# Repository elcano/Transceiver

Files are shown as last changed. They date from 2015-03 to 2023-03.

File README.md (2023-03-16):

# Transceiver
Hardware and software to support Transmit/Receive boards

The Elcano Project is an autonomous vehicle control system that runs on a stack of microprocessors, with no operating system and 
no machine learning.
Files that span more than one processor are kept in Elcano/General. The other repositories are:
Elcano/LowLevel – Drive by wire
Elcano/HighLevel – Localization, Route Finding and Pilot
Elcano/Sonar – Detects obstacles from ultrasonic sensors
Elcano/Sweep – Scanse Sweep Lidar for Obstacle Detection
Elcano/QDED – Quadrature Edge Detectors for machine vision
Elcano/Transceiver – Transmit and receive boards for remote control option

The primary autonomous vehicle control comes from HighLevel. Alternatively, the vehicle can be controlled manually, which is the function 
of the Tranceiver board. Depending on what is soldered into the board and which software is used, there are several configurations of the 
transceiver:
 
Transmitter board with joysticks and switches sending via radio.
Receiver board receiving from radio and putting information on CAN bus.
Transmitter via Bluetooth.
Receiver via Bluetooth.
Receiver from a hobbyist RC controller
User interface with joysticks and switches, putting information on CAN bus.

### Required libraries:

#### *Seeed-Studio/CAN-BUS-Shield*
Download as zip from https://github.com/Seeed-Studio/Seeed_Arduino_CAN. 
In Arduino IDE, go to Sketch -> Include Library -> Add .ZIP Library and select the .zip folder.

#### *elcano/Elcano_C2_LowLevel/Can_Protocol.h*
Download “Can_Protocol.h” from https://github.com/elcano/elcano/tree/master/Elcano_C2_LowLevel. 
Create a folder in the location where the Arduino IDE contains it’s libraries on your computer and add this file to the newly created folder.

#### *http://www.airspayce.com/mikem/arduino/RadioHead/classRH__RF69.html*
Download as zip from http://www.airspayce.com/mikem/arduino/RadioHead/index.html. 
In Arduino IDE, go to Sketch -> Include Library -> Add .ZIP Library and select the .zip folder.

#### *elcano/libraries/Settings/SettingsTemplate.h*
Download “SettingsTemplate.h” from https://github.com/elcano/elcano/tree/master/Elcano_C2_LowLevel. 
Create a folder in the location where the Arduino IDE contains it’s libraries on your computer and add this file to the newly created folder.

#### *scanse/sweep-arduino/tree/master/Sweep*
Download as zip from https://github.com/scanse/sweep-arduino. 
Note: need to unzip zip folder and then compress to zip only the sweep folder.
In Arduino IDE, go to Sketch -> Include Library -> Add .ZIP Library and select the .zip folder.

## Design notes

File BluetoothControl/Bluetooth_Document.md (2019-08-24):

# Bluetooth Modules:

###Bluetooth Transmitter
**Hardware Setup:**
1. Sparkfun SAMD21 Mini Breakout
1. HC-05 Bluetooth Modules (Master)
1. Parallax 2-Axis Joystick
1. Power supply
1. USB cable

| SPARKFUN SAMD21 MINI BREAKOUT  | PARALLAX 2-AXIS JOYSTICK | HC-05 Bluetooth  | 
| :---: | :---: | :---: |
| Pin 1 (TX) | | RX | 
| Pin 0 (RX) | | TX | 
| GND (ground) | GND (ground | GND (ground) | 
| VCC (5V) | L/R+ && U/D+ (5V) | VCC (5v) | 
| D8 (8) | | STATE | 
| D9 (9) | | EN | 
| A2 | U/D | |
| A3 | L/R | |

Bluetooth Transmitter Image Transmitter

**Software Setup:**
Bluetooth Transmitter .ino file
```c++
#include "BluetoothControlTx.h"

// initialize package
transmitterData transmitterDat;
// Utilities variables
unsigned long currTime = 0;
unsigned int counter = 0;
// Data/Buffer variables
String logger;
String dataSent;
char ackMessage; // received from the RX when it got the package
char dataBuffer[BUFFER_LIMIT];
char ackBuffer[ACK_LIMIT];

void setup()
{
    // Init hardware serial port --> PIN: 0 (RX) | 1 (TX)
    Serial1.begin(UART_BAUDRATE);
    SerialUSB.begin(UART_BAUDRATE); // Serial Monitor
    if (DEBUG)
        // wait until SerialUSB initialize
        while (!SerialUSB)
            ;

    String initMesg = "** TranX Init at " + String(UART_BAUDRATE);
    SerialUSB.println(initMesg);
    SerialUSB.println("Setup Complete!");
}

void loop()
{
    readInputs();

    // Send the values to through Bluetooh module
    String str = 'T' + String(transmitterDat.turn) + 'F' + String(transmitterDat.throttle) 
    + 'A' + String(transmitterDat.autonomous) + 'E' + String(transmitterDat.ebrake) 
    + 'R' + String(transmitterDat.reverse) + '@';
    str.toCharArray(dataBuffer, BUFFER_LIMIT);

    for (int i = 0; i < BUFFER_LIMIT; i++)
    {
        Serial1.write(dataBuffer[i]);
        SerialUSB.write(dataBuffer[i]);
    }
    SerialUSB.println();
    // Read from Bluetooh module and send to Arduino Serial Monitor
    // (Receiving ACK message from the RX)
    while (Serial1.available() > 0)
    {
        if (DEBUG)
        {
            ackMessage = Serial1.read();
            ackBuffer[counter] = ackMessage;
            counter++;
            dataBuffer[counter] = '\0'; // Keep the string NULL terminated
            SerialUSB.print(logger);
            if (ackMessage == '@') {
                break;
            }
        }
    }
    counter = 0;
    waitForProcess(100);
}

/**
 * --------------------- Helper Functions --------------------------------
 */
void readInputs()
{
    transmitterDat.turn = analogRead(TURN_PIN);
    transmitterDat.throttle = analogRead(THROTTLE_PIN);
    transmitterDat.autonomous = digitalRead(AUTO_PIN);
    transmitterDat.ebrake = digitalRead(EBRAKE_PIN);
    transmitterDat.reverse = digitalRead(REVERSE_PIN);
}

// Better version of delay() in Arduino Lib
void waitForProcess(long interval)
{
    currTime = millis();
    while (millis() < currTime + interval)
    {
        ; // Wait for "interval" ms to ensure packages are received
    }
}
```

Bluetooth Transmitter .h file
```c++
// Arduino Serial Port 
#define UART_BAUDRATE 9600 // The current TX has to be at 9600 Baurd rate so that the RX can read the data at 38400 Buard rate --- This is off, but it works for now.
#define BUFFER_LIMIT 20
#define ACK_LIMIT 5

// transmitter input pins
#define TURN_PIN A3     // joystick 2 L/R
#define THROTTLE_PIN A2 // joystick 1 U/D
#define INTERRUPT_PIN 2
#define AUTO_PIN 5
#define EBRAKE_PIN 4
#define REVERSE_PIN 20

#define NO_PACKAGE -1 // No package received
#define DEBUG 1       // Prints debugging info to serialUSB, can impact loop time                        
                      // WARNING: when true (!0), you must connect USB to allow hardware reset, otherwise
                      // SAMD21 Arduino will do nothing*/

typedef struct
{
    unsigned int throttle;
    unsigned int turn;
    bool ebrake;
    bool autonomous;
    bool reverse; // Future Stuff
} transmitterData;
```

###Bluetooth Receiver
**Hardware Setup:**
1. Sparkfun SAMD21 Mini Breakout
1. HC-05 Bluetooth Modules (Slave)
1. Power supply
1. USB cable

|  HC-05 Bluetooth | SPARKFUN SAMD21 MINI BREAKOUT  |
| --- | :---: |
| RX | Pin 1 (TX) |
| TX | Pin 0 (RX) |
| GND (ground) | GND (ground) |
| VCC (5v) | VCC (5V) |
| STATE | |
| EN | |

**Software Setup:**
Bluetooth Transmitter .ino file
```c++
#include "BluetoothControlRx.h"
//#include "Can_Protocol.h"
//#include <mcp_can.h> // using mcp_can lib from Seeed Studio

// Core Variables
receiverData receiverDat;
//MCP_CAN CAN(49); // chip selection pin for CAN. 53 for mega, 49 for our new low level board

// Utilities variables
unsigned long currTime = 0;
int turnCounter = 0;
int throttleCounter = 0;

// Data/Buffer variables
String logger;
char turnBuffer[BUFFER_LIMIT]; // char is similar to unsigned char --> which is a byte
char throttleBuffer[BUFFER_LIMIT];
char ackBuffer[ACK_LIMIT];
char dataChar;
char dividerChar;

void setup()
{
//    logger = "ACK@";
//    logger.toCharArray(ackBuffer, ACK_LIMIT);

    // Init hardware serial port --> PIN: 0 (RX) | 1 (TX)
    Serial1.begin(UART_BAUDRATE);
    SerialUSB.begin(UART_BAUDRATE); // Serial Monitor

    if (DEBUG)
        // wait until SerialUSB initialize
        while (!SerialUSB)
            ;

    // Inital CAN bus with 500KBPS baud rate (CAN_500KBPS is the baud rate)
    //    while (CAN_OK != CAN.begin(CAN_500KBPS))
    //    {
    //        if (DEBUG)
    //        {
    //            SerialUSB.println("CAN BUS Shield init fail");
    //            SerialUSB.println("Re-initializing...");
    //        }
    //        delay(1000);
    //    }

    if (DEBUG)
    {
        SerialUSB.println("CAN BUS init ok!");
        String initMesg = "** RecX Init at " + String(UART_BAUDRATE);
        SerialUSB.println(initMesg);
        SerialUSB.println("Setup Complete!");
    }
}

void loop()
{
    // Checks whether data is comming from the serial port
    while (Serial1.available() > 20)
    {
        processComingData();
        if (DEBUG)
        {
            String str = "Parsed value: T" + String(receiverDat.turn) + " F" + String(receiverDat.throttle) + " A" + String(receiverDat.autonomous) + " E" + String(receiverDat.ebrake) + " R" + String(receiverDat.reverse) + " @";
            SerialUSB.println(str);
        }
             transferToCanBus();
             //    ackMessage();
    }

}

/**
 * --------------------- Helper Functions --------------------------------
 */

// Gather/Process data and put it into dataBuffer buffer for parsing
void processComingData()
{
    dataChar = Serial1.read(); // Reads the data from the serial port
    dataParser();
}

// Parse the completed data buffer from the transmitter
void dataParser()
{

    if (dataChar == 'T' || dataChar == 'F' || dataChar == 'A' || dataChar == 'E' || dataChar == 'R' || dataChar == '@')
    {
        dividerChar = dataChar;
    }

    // Start parsing data byte
    if ((dividerChar == '@') || (dividerChar != dataChar))
    {
        switch (dividerChar)
        {
        case 'T': // Parsing Turn
            if (DEBUG_PARSE)
                SerialUSB.println("T - " + String(dataChar));
            turnBuffer[turnCounter] = dataChar;
            turnCounter++;
            turnBuffer[turnCounter] = '\0'; // Keep the string NULL terminated
            break;
        case 'F': // Parsing Throttle
            if (DEBUG_PARSE)
                SerialUSB.println("F - " + String(dataChar));
            throttleBuffer[throttleCounter] = dataChar;
            throttleCounter++;
            throttleBuffer[throttleCounter] = '\0'; // Keep the string NULL terminated
            break;
        case 'A': // Parsing Autonomous
            if (DEBUG_PARSE)
                SerialUSB.println("A - " + String(dataChar));
            if (dataChar == '1')
                receiverDat.autonomous = true;
            else
                receiverDat.autonomous = false;
            break;
        case 'E': // Parsing Ebrake
            if (DEBUG_PARSE)
                SerialUSB.println("E - " + String(dataChar));
            if (dataChar == '1')
                receiverDat.ebrake = true;
            else
                receiverDat.ebrake = false;
            break;
        case 'R': // Parsing Reverse
            if (DEBUG_PARSE)
                SerialUSB.println("R - " + String(dataChar));
            if (dataChar == '1')
                receiverDat.reverse = true;
            else
                receiverDat.reverse = false;
            break;
        case '@': // Reaching the end of line
            if (dataChar == '@')
            {
                if (DEBUG_PARSE)
                    SerialUSB.println("EOT - " + String(dataChar));

                // update turn and throttle struct
                receiverDat.turn = atoi(turnBuffer);
                receiverDat.throttle = atoi(throttleBuffer);

                // reset all counter and buffer
                turnCounter = 0;
                throttleCounter = 0;
                turnBuffer[turnCounter] = NULL;
                throttleBuffer[throttleCounter] = NULL;
            }
            break;
        default:
            if (DEBUG_PARSE)
                SerialUSB.println("Default - " + String(dataChar));
            break;
        }
    }
}

// Process the data over the CAN BUS protocal
void transferToCanBus()
{
    if (DEBUG)
    {
        SerialUSB.println("Sending data to CAN BUS...");
    }

    //    CAN.sendMsgBuf(RCDrive_CANID, 0, BUFFER_LIMIT, (char *)&receiverDat); // RCDrive_CANID or RCStatus_CANID i dont know...
    //    wait(100);
}

// ACKNOWLEDGE the data received
void ackMessage()
{
    SerialUSB.println();
    if (Serial1.available())
    {
        Serial1.print("ACK");
    }
}

// Better version of delay() in Arduino Lib
void wait(long interval)
{
    currTime = millis();
    while (millis() < currTime + interval)
    {
        ; // Wait for "interval" ms to ensure packages are received
    }
}

```

Bluetooth Receiver .h file
```c++
// Arduino Serial Port 
#define UART_BAUDRATE 38400
#define BUFFER_LIMIT 20
#define ACK_LIMIT 5

// Arduino Debugger
#define NO_PACKAGE -1 // No package received
#define DEBUG_PARSE 0 // This debug only for process coming data function
#define DEBUG 1       // Prints debugging info to serialUSB, can impact loop time                        
                      // WARNING: when true (!0), you must connect USB to allow hardware reset, otherwise
                      // SAMD21 Arduino will do nothing*/

// Data struct of packages being sent
typedef struct
{
    unsigned int throttle;
    unsigned int turn;
    bool ebrake;
    bool autonomous;
    bool reverse; // Future Stuff
} receiverData;

#define RCStatus_CANID 0x50
#define HiStatus_CANID 0x100
#define LowStatus_CANID 0x200
#define RCDrive_CANID 0x300
#define HiDrive_CANID 0x350
#define Actual_CANID 0x500
```

### References/Tip
1. Sparkfun SAMD21 Mini Breakout hook up guide: https://learn.sparkfun.com/tutorials/samd21-minidev-breakout-hookup-guide/samd21-mini-breakout-overview
1. If the receiver gets a reverse question mark, it might because of both the receiver and the transmitter Baud Rate are not configured at the same rate. Please try Baud Rate: 38400 (on the Receiver) and 9600 (on the Transmitter) and vice versa to see if the outcome is any better.

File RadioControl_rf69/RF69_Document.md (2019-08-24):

# Note for future implementations:
1. If the board got an error or undetectable by any computer after uploading the code, **__Double Click the reset button__** at the end of the SAMD21 Module to refresh the whole board.

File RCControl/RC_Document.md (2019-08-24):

# RC Modules Documentation

**Hardware Setup for RC Receiver:**
Required hardware: 
1. Sparkfun SAMD21 Mini Breakout
2. Spektrum AR610X Receiver
3. Power supply
4. USB cable

| SPEKTRUM AR610X  | SPARKFUN SAMD21 MINI BREAKOUT  |
| --- | :---: |
| AUX1 | 7 |
| GEAR | 8 |
| RUDD | 0 |
| ELEV | 1 |
| AILE | 6 |
| THRO | 9 |
| BND/BRA | NA (Use for Binding only) |

The RC code utilizes the `attachInterrupt()` from Arduino to detect different in frequency that the board is receiving while the controller values change. This is almost similar to an `async` which will optimize the code so that we won't have to constantly check for data every iteration in the `loop()`.

Whenever the RC receiver gets a signal, the value will go high and activate the `attachInterrupt()` to keep track when the value return back to low. Once it completed this step, the time period where the change is recordeded will be the value of each switches on the Receiver channels.

# Note for future implementations:
1. The CAN BUS Protocol is written with the RC code; however, the CAN BUS has yet been tested at this moment. Recommend finding a way to test current CAN BUS connection for the RC code.
2. There is a __Note__  section in the main `Loop()` of the RCControlRx.ino. This Note is there for the future implementation where the CAN BUS passed the data to other Low/High level board and received the ACK message back. Without setting the `receiverData.newData = false;` the RC code might not be able to receive new data coming from the RC controller. 
3.

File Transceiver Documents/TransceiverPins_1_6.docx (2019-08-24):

Elcano Transceiver Board

Arduino | Bluetooth | RC receiver | Rfm69rcw Radio | CAN 2515 | Receiver Controls | Transmitter Controls
D0 RX | RX1 | CH3_A
D1 TX | TX0 | CH4_A
D2 | | | | CAN_INT
D3 | | | | CAN_SS
D4 | | | | | E-stop | E-stop
D5 | | | | | Manual/Auto | Manual/Auto
D6 | | CH5_A | Radio OK LED | | | Radio Ok led
D7 | MOD | CH1_A
D8 | CTS | CH2_A
D9 | RTS | CH6_A
D10 SS | | | Radio_SS
D11 MOSI | | | MOSI | MOSI
D12 MISO | | | MISO | MISO
D13 SCK | | | SCK | SCK
D20 | | | | | Reverse | Reverse
D21 | | | Radio Interrupt
A0 | | | | | 2 Up-Dn / Center
A1 | | | | | 1 L-R / center | 1 L-R / center
A2 | | | | | 1 Joystick Up-Dn | 1 Joystick Up-Dn
A3 | | | | | 2 Joystick L-R | 2 Joystick L-R
RESET | | | Reset | | | Reset sw
Vin (5V)
Vcc (3.3V) | Vin = 3.3V | 3.3V | 3.3V | 3.3V | 3.3V | 3.3V
GND | GND | GND | GND | GND | GND | GND
AREF to 3.3V

Gray shaded columns are mutually exclusive; so are blue shaded columns.

Transmitter board will not have CAN or RC receiver. Transmitter switches shall incorporate LEDs that indicate their state.
Receiver may have all components, but normally will use only one of Radio, Bluetooth or RC receiver.

Arduino: Sparkfun SAMD21: https://www.sparkfun.com/products/13664

Radio: SparkFun parts 12775, 14875, 592: https://www.sparkfun.com/products/12775 ,
http://www.orcam.eu/res/Datablad/rf69v12.pdf

Bluetooth: Adafruit Bluefruit: https://www.adafruit.com/product/2479?gclid=EAIaIQobChMI_Iv29-CR4AIVi8JkCh0fKwybEAYYASABEgKXWfD_BwE

RC Receiver: Spektrum AR610: https://spektrumrc.com/Products/Default.aspx?ProdId=SPM6700

Level shifter: https://www.addicore.com/TXS0108E-p/ad284.htm

An equivalent level shifter is https://www.adafruit.com/product/395?gclid=EAIaIQobChMIk7nvup_Q4AIVER6tBh0WywndEAQYAiABEgJw7fD_BwE

CAN: MCP 2515 http://ww1.microchip.com/downloads/en/devicedoc/21801e.pdf and
MCP 2551 http://ww1.microchip.com/downloads/en/devicedoc/21667d.pdf

Controls: Two joysticks and three toggle switches. Toggle switches have built-in LEDs to show their state. There is also an LED connected to power.

Bluetooth and RC Receiver use separate physical socket:
Bluetooth 8 pins: Mod, CTS, TX0, RX1, Vin, RTS, GND, DFU

RC receiver 7 pins: Ch1, Ch2, Ch3, Ch4, Ch), Ch6, BND
RC receiver also has 7 rows of power and 7 rows of ground forming a 3x7 socket.

Pin view is top view of the transceiver board or bottom view of RC Receiver

Gnd | Gnd | Gnd | Gnd | Gnd | Gnd | Gnd
5V | 5V | 5V | 5V | 5V | 5V | 5V
Ch1_B | Ch2_B | Ch3_B | Ch4_B | Ch5_B | Ch6_B | BND

ChX Signals from RC Receiver will need to be converted from 5V to 3.3V. This is the only voltage conversion needed on the transceiver board. At present, neither of the receivers will bind or respond to the Spektrum transmitter.

The level shifter is connected with VB to 5V, and VA and OE to 3.3V. On the level shifter, channels A 1-6 are 3.3V signals connected to the Arduino. Channels B 1-6 are 5V signals connected to the RC receiver socket. Channels 7 and 8 are not used.

There is a jumper to set the Radio reset to either D6 or Arduino RESET.

~~JB:~~ ~~tx~~ ~~and~~ ~~rx~~ ~~sketch resets RF69 radio on D6 but radio reset should not connect electrically to Arduino reset so we can~~ ~~perform a radio reset in software by toggling the pin.~~
D6 is jumpered to either Radio OK LED or RC Receiver CH5.

There may be two joysticks. Jumpers select which axes are used. There are several configurations

1. Up to two joysticks that do not return a center value. Software may choose to process only the left-right reading from one and only the up-down reading from the other.
1. Two joysticks returning center values. One produces a left-right reading and the other produces up-down.
2. A single joystick returning a center value, a left-right, and an up-down signal.

Board has an input jack for 9 to 12V DC, which is put through regulators to produce 5V and 3.3V. All parts (except RC receiver) run from 3.3V. The 2551 will use 5V for CAN transmission.

CANRX and CAN_RXD are the same. CANTX and CAN_TXD are the same.
The signals CANH and CANL are the outputs to the CAN bus connector.

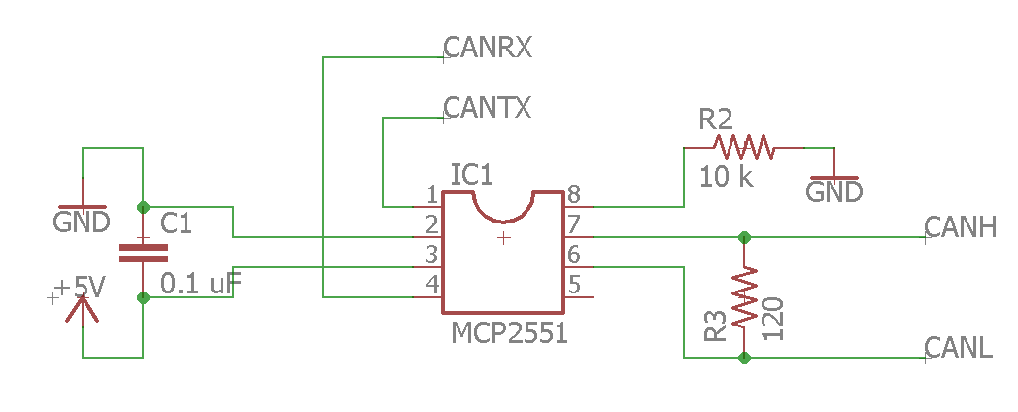
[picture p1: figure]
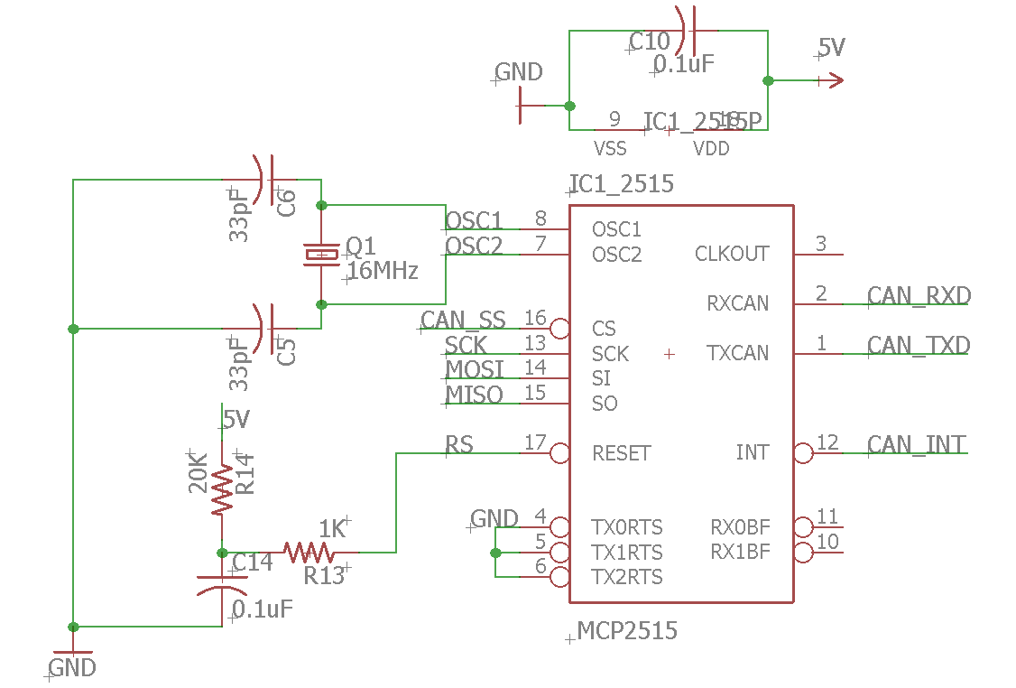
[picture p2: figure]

Rev 1.6 Feb 22, 2019

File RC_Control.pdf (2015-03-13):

# RC Control

# CSS 427: Final Report

## Brad Minogue, Carl Martinez, Amit Moolani, Alexander Yelle, Enoch Fu

Implementation of a remote control subsystem for an Elcano tricycle.

# RC Control

## CSS 427: Final Report

# Introduction

This project led to the implementation of a remote control subsystem for use on an Elcano tricycle. Using the knowledge and experience that we gained in previous labs and lectures we were able to fully integrate a remote control into the steering, accelerating, and braking of an Elcano tricycle. An Arduino with a DAC connected acted as the gateway from the RC receiver to the servo-motor and

## throttle. The process took 3 weeks to complete, each week accomplishing a different goal:

1. Adding throttle connectivity to the trike.
2. Writing and testing code to translate RC input data to correct PWM signals.
3. Hooking up the Arduino to the trike, testing functionality.

# Problems Addressed

## - Adding Throttle Capability

## The project started with troubleshooting the throttle connection on the trike. Everything

appeared to be wired correctly but we would get no response from the throttle. We had to test every connection and power source to find the root of the problem. After testing all existing

## connections and finding nothing wrong we had to turn to the manual to find out why the throttle was not working. The end result was that the control power supply pin was not

connected. After making the appropriate connection the trike gained throttle capabilities.

## - RC Receiver Connection

We used the left joystick from the RC receiver to receive input for acceleration, steering and braking. Right and left for steering, forward and backward for acceleration and braking. Attaching the RC receiver to an Arduino allowed us to translate the inputs into a PWM signal to control the servo-motor and throttle. We wrote code to make a linear translation from RC

## input to the PWM signal. A DAC was attached to the Arduino to allow for correct throttle

output.

## - Calibration of Input and Output

Using existing code we already had the range of numbers for the output values. The RC input required testing to find the maximum and minimum values for steering, braking, accelerating, and how large the dead zone should be.

## - Bike Connections

## We then were able to connect our programmed Arduino to the shield connected to the yellow

trike. The trike had battery packs to provide the Arduino and motors with power.

## Connections existed from the motors to a breadboard that sat on the trike. After reading through schematics and checking connections with the previous setup, we connected our RC

receiver to get power from the Arduino’s 5V output. We also connected the Channels 1 and 2 from the receiver to be read into pins 2 and 3 of the Arduino. These gave the RC transmitted the ability to control the steering and braking of the trike respectively. We then connected the motor’s steering and braking input pins to the Arduino’s steering and braking output pins.

## These were pins 6 and 7 on the Arduino respectively. Then the throttle wires had to be

snipped and connected to the 5V and GND pins of the Arduino. The input for the throttle was

## connected to the Arduino via pin 12 on the 15 pin DAC. Once those connections were made

and the trike was fastened and powered up, we were able to confirm the working of our trike.

## - Brakes

The braking system of the trike had been manipulated in the past, restricting its functioning. We were able to find the loose connection in the brake that did not allow the brake to ever

## fully compress over the wheel to give it adequate braking. We attempted to fix this by tightening the brake wires and moving the location of the pivot holding the brakes to the brake system motor. After an hour and a half of debugging we were able to mildly improve

the system, but still needs much more work to be able to work to the full of its capability.

# Code

//RC_Control.ino
#include <SPI.h>

//RC input values
const int DEAD_ZONE = 75;
const int ACC_START = 1322; const int TURN_START= 1322; //max brake
const int MIN_ACC = 911;
//full throttle
const int MAX_ACC = 1730;
//max turn left
const int MIN_TURN = 911;
//max turn right
const int MAX_TURN = 1733;

//OUTPUT values
const int MIN_ACC_OUT = 40; const int MAX_ACC_OUT = 227;

const int MIN_BRAKE_OUT = 167; const int MAX_BRAKE_OUT = 207;

const int LEFT_TURN_OUT = 126; const int RIGHT_TURN_OUT = 250; const int STRAIGHT_TURN_OUT = 187;

//ARDUINO PIN SELECTORS
const int TURN_PIN = 2;
const int ACC_PIN =3;
const int ACC_OUT_PIN = 5;
const int STEER_OUT_PIN = 6;
const int BRAKE_OUT_PIN = 7;
const int SelectCD | = 49; // Select IC 3 DAC (channels C and D)
const int SelectAB | = 53; // Select IC 2 DAC (channels A and B)

void setup()
{ //Set up pins
pinMode(ACC_OUT_PIN, OUTPUT);
pinMode(BRAKE_OUT_PIN, OUTPUT); pinMode(STEER_OUT_PIN, OUTPUT);
// SPI: set the slaveSelectPin as an output: pinMode (SelectAB, OUTPUT);
pinMode (SelectCD, OUTPUT);
pinMode (10, OUTPUT);

SPI.setDataMode( SPI_MODE0);
SPI.setBitOrder( MSBFIRST);
// initialize SPI:
// The following line should not be neccessary. It uses a system library. PRR0 &= ~4; // turn off PRR0.PRSPI bit so power isn't off
SPI.begin();
for (int channel = 0; channel < 4; channel++)
DAC_Write (channel, 0); // reset did not clear previous states

Serial.begin(9600);
}
//Checks for each input: accelerating, turning, braking
void loop() {
//Steering
int test = pulseIn(TURN_PIN, HIGH,25000); if(testTurn(test))
{
//Serial.print("turn: ");
//Serial.println(convertTurn(test)); steer(convertTurn(test));
}
else
{
steer(STRAIGHT_TURN_OUT);
}
//Braking
test = pulseIn(ACC_PIN, HIGH,25000); if(testBrake(test))
{
//Serial.print("braking: "); //Serial.println(convertBrake(test)); brake(convertTurn(test));
}
else
{
brake(MIN_BRAKE_OUT);
}
//Accelerating
if(testAcc(test))
{
//Serial.print("Acc: ");
//Serial.println(convertThrottle(test)); moveVehicle(test);
}
else
{
moveVehicle(MIN_ACC_OUT);
}
delay(50);
}
//Converts RC values to corresponding values for the DAC int convertTurn(int input)
{
//full turn right = 250, full turn left = 126
int dacRange = RIGHT_TURN_OUT - LEFT_TURN_OUT; int rcRange = MAX_TURN - MIN_TURN;
input-= MIN_TURN;
double output = (double)input /(double)rcRange; //swap left and right
output = 1 - output;
output *= dacRange;
output += LEFT_TURN_OUT;
//set max and min values if out of range int trueOut = (int)output;
if(trueOut > RIGHT_TURN_OUT)
trueOut = RIGHT_TURN_OUT;
else if(trueOut < LEFT_TURN_OUT) trueOut = LEFT_TURN_OUT;
return trueOut;

}
int convertBrake(int input)
{
//full brake = 207, min = 167
const int dacRange = MAX_BRAKE_OUT - MIN_BRAKE_OUT; const int rcRange = (ACC_START - DEAD_ZONE) - MIN_ACC; input -= MIN_ACC;
double output = (double)input /(double)rcRange; output *= dacRange;
output += MIN_BRAKE_OUT;
//set min values if out of range
int trueOut = (int)output; if(trueOut < MIN_BRAKE_OUT) trueOut = MIN_BRAKE_OUT;
return trueOut;
}
int convertThrottle(int input)
{
//full throttle = 227, min = 40
const int dacRange = MAX_ACC_OUT - MIN_ACC_OUT; const int rcRange = MAX_ACC - (ACC_START + DEAD_ZONE); input -= (ACC_START + DEAD_ZONE);
double output = (double)input /(double)rcRange; output *= dacRange;
output += MIN_ACC_OUT;
//set max values if out of range
int trueOut = (int)output; if(trueOut > MAX_ACC_OUT)
trueOut = MAX_ACC_OUT;
return trueOut;
}

//Tests for inputs
boolean testTurn(int turn)
{
return (turn > ACC_START + DEAD_ZONE || turn < ACC_START - DEAD_ZONE); }
boolean testAcc(int acc)
{
return (acc > ACC_START + DEAD_ZONE); }
boolean testBrake(int brake)
{
return (brake < ACC_START - DEAD_ZONE); }
//Send values to output pin
void steer(int pos)
{
analogWrite(STEER_OUT_PIN, pos); }
void brake(int amount)
{
analogWrite(BRAKE_OUT_PIN, amount); }
void moveVehicle(int acc)
{
/* Observed behavior on ElCano #1 E-bike no load (May 10, 2013, TCF)
0.831 V at rest | 52 counts
1.20 V: nothing | 75
1.27 V: just starting 79
1.40 V: slow, steady 87
1.50 V: brisker | 94
3.63 V: max | 227 counts
255 counts = 4.08 V
*/
DAC_Write(0, acc);
}
/*---------------------------------------------------------------------------------------*/ /* DAC_Write applies value to address, producing an analog voltage.

// address: 0 for chan A; 1 for chan B; 2 for chan C; 3 for chan D // value: digital value converted to analog voltage
// Output goes to mcp 4802 Digital-Analog Converter Chip via SPI // There is no input back from the chip.
*/
void DAC_Write(int address, int value)

/*
REGISTER 5-3: WRITE COMMAND REGISTER FOR MCP4802 (8-BIT DAC) A/B — GA SHDN D7 D6 D5 D4 D3 D2 D1 D0 x x x x
bit 15 | bit 0
bit 15 | A/B: DACA or DACB Selection bit
1 = Write to DACB
0 = Write to DACA
bit 14 | — Don’t Care
bit 13 | GA: Output Gain Selection bit
1 = 1x (VOUT = VREF * D/4096)
0 = 2x (VOUT = 2 * VREF * D/4096), where internal VREF = 2.048V.
bit 12 SHDN: Output Shutdown Control bit
1 = Active mode operation. VOUT is available.
0 = Shutdown the selected DAC channel. Analog output is not available at the channel that was shut down.
VOUT pin is connected to 500 k (typical)
bit 11-0 D11:D0: DAC Input Data bits. Bit x is ignored.

With 4.95 V on Vcc, observed output for 255 is 4.08V.
This is as documented; with gain of 2, maximum output is 2 * Vref

*/

{
int byte1 = ((value & 0xF0)>>4) | 0x10; // acitve mode, bits D7-D4
int byte2 = (value & 0x0F)<<4; | // D3-D0
if (address < 2)
{
// take the SS pin low to select the chip: digitalWrite(SelectAB,LOW);
if (address >= 0)
{
if (address == 1)
byte1 |= 0x80; // second channnel SPI.transfer(byte1);
SPI.transfer(byte2);
}
// take the SS pin high to de-select the chip: digitalWrite(SelectAB,HIGH);
}
else
{
// take the SS pin low to select the chip: digitalWrite(SelectCD,LOW);
if (address <= 3)
{
if (address == 3)
byte1 |= 0x80; // second channnel SPI.transfer(byte1);
SPI.transfer(byte2);
}
// take the SS pin high to de-select the chip: digitalWrite(SelectCD,HIGH);
}
}

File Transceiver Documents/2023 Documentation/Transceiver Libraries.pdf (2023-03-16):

Transceiver Libraries Required

This document outlines the required libraries for each .ino file in the Transceiver repository. A list of all required libraries and links with instructions for download are shown below, as well as an in-depth specification for each .ino file. The github for these files can be found here https://github.com/elcano/Transceiver with current changes found here https://github.com/jacrys3/Transceiver.

Required libraries:
Seeed-Studio/CAN-BUS-Shield
Download as zip from https://github.com/Seeed-Studio/Seeed_Arduino_CAN
In Arduino IDE, go to Sketch -> Include Library -> Add .ZIP Library and select the .zip folder

elcano/Elcano_C2_LowLevel/Can_Protocol.h
Download “Can_Protocol.h” from https://github.com/elcano/elcano/tree/master/Elcano_C2_LowLevel
Create a folder in the location where the Arduino IDE contains it’s libraries on your computer and add this file to the newly created folder.

http://www.airspayce.com/mikem/arduino/RadioHead/classRH__RF69.html
Download as zip from http://www.airspayce.com/mikem/arduino/RadioHead/index.html
In Arduino IDE, go to Sketch -> Include Library -> Add .ZIP Library and select the .zip folder

elcano/libraries/Settings/SettingsTemplate.h
Download “SettingsTemplate.h” from https://github.com/elcano/elcano/tree/master/Elcano_C2_LowLevel
Create a folder in the location where the Arduino IDE contains it’s libraries on your computer and add this file to the newly created folder.

scanse/sweep-arduino/tree/master/Sweep
Download as zip from https://github.com/scanse/sweep-arduino
Note: need to unzip zip folder and then compress to zip only the sweep folder
In Arduino IDE, go to Sketch -> Include Library -> Add .ZIP Library and select the .zip folder

BluetoothControlRx.ino
Seeed-Studio/CAN-BUS-Shield
elcano/Elcano_C2_LowLevel/Can_Protocol.h

BluetoothControlTx.ino
None

lidar.ino
Seeed-Studio/CAN-BUS-Shield elcano/Elcano_C2_LowLevel/Can_Protocol.h scanse/sweep-arduino/tree/master/Sweep

RadioControl_rf69.ino
http://www.airspayce.com/mikem/arduino/RadioHead/classRH__RF69.htmlSeeed-Studio/CAN-BUS-Shield

RCControlRx.ino
Seeed-Studio/CAN-BUS-Shield elcano/Elcano_C2_LowLevel/Can_Protocol.h elcano/libraries/Settings/SettingsTemplate.h

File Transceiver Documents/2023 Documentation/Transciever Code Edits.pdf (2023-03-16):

Transceiver Code Edits

This document contains any edits made to the Transceiver code given in https://github.com/elcano/Transceiver. These changes can be seen respectively in https://github.com/jacrys3/Transceiver.

BluetoothControlRx.ino - Compiles
1. All uses of “SerialUSB” have been changed to “Serial3”
2. Fixed an issue where some semi-colons were missing when pre-declaring functions “sendToCanBus” and “receiveFromCanBus”
3. Creation of CAN object needs to be of type “mcp2515_can”, not “MCP_CAN”
4. In sendToCanBus() method, need to reference MCP_CAN when using sendMsgBuff
5. Need to include “mcp2515_can.h” and “mcp2515_can_dfs.h”

BluetoothControlTx.ino - Compiles
1. All uses of “SerialUSB” have been changed to “Serial3”

Lidar.ino - Compiles
1. All uses of “lidarMSGBuffer” have been changed to “lidarStruct”
2. Creation of CAN object needs to be of type “mcp2515_can”, not “MCP_CAN”
3. In sendToCanBus() method, need to reference MCP_CAN when using sendMsgBuff
4. Need to include “mcp2515_can.h” and “mcp2515_can_dfs.h”

RadioControl_rf69.ino - Compiles
1. All uses of “SerialUSB” have been changed to “Serial3”
2. All uses of “analogReadResolution” have been changed to “analogRead”
3. RH_RF69 has been changed to RC_RF69_H
4. Creation of CAN object needs to be of type “mcp2515_can”, not “MCP_CAN”
5. Need to include “mcp2515_can.h” and “mcp2515_can_dfs.h”

RCControlRx.ino - Compiles
1. All uses of “SerialUSB” have been changed to “Serial3”
2. Creation of CAN object needs to be of type “mcp2515_can”, not “MCP_CAN”
3. In sendToCanBus() method, need to reference MCP_CAN when using sendMsgBuff
4. Need to include “mcp2515_can.h” and “mcp2515_can_dfs.h”

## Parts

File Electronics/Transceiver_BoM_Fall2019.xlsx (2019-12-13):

 |  | Board Manufacturer Specs | rvc RC | xmit BT | rcv BT | xmit radio | rcv radio
 | Traces are 15 mil | Board needs 2 oz copper |  |  |  |  |  |  | Two Layers: Front & Back
 |  | Through hole components
Qty | Device Name | Value |  |  |  |  |  | In BoM? | Digikey Part Number | Package | Part Label | Description | DESCRIPTION | External Link | DIGI-KEY_PURCHASE_URL | MANUFACTURER_PART_NUMBER | MF | MP | MPN | OC_FARNELL | OC_NEWARK | PACKAGE | PROD_ID | SF_SKU | SPICEPREFIX | VALUE | VENDOR
5 | PINHD-1X2 | SAMD21 | 1 | 1 | 1 | 1 | 1 | yes | 732-5315-ND | 1X02 | 5V TEST,3.3V TEST, JUMPER, RADIO-OK | PIN HEADER |  |  | https://www.digikey.com/products/en?keywords=732-5315-ND
5 | PINHD-1X3 | Rcvr (Pwr/Reset) XMIT+(auto/E_stop/Rev) 2 |  | 5 | 2 | 5 | 2 | yes | 732-5316-ND | 1X03 | REST SW,POWER SW,AUTO MNL,ESTOP,REVERSE | PIN HEADER |  |  | https://www.digikey.com/products/en?keywords=%20732-5316-ND
2 | PINHD-1X4 | JoyStick L/R | 0 | 2 | 0 | 2 | 0 | yes | 732-5317-ND | 1X04 | LEFT JOY STICK, RIGHT JOYSTICK | PIN HEADER |  |  | https://www.digikey.com/products/en?keywords=732-5317-ND
2 | PINHD-1X6 | BLUETOOTH Module | 0 | 1 | 1 | 0 | 0 | yes | S5481-ND | 1X06 | HC-05 BLUETOOTH | PIN HEADER | Right Angle Female PIN Header |  | https://www.digikey.com/product-detail/en/sullins-connector-solutions/PPPC061LGBN-RC/S5481-ND/775939
3 | PINHD-1X7 | RC rcvr | 3 | 0 | 0 | 0 | 0 | yes | S7040-ND | 1X07 | RC-RECEIVER | PIN HEADER | Female pin header |  | https://www.digikey.com/product-detail/en/sullins-connector-solutions/PPPC071LFBN-RC/S7040-ND/810179
2 | PINHD-1X8 | RF Module | 0 | 0 | 0 | 2 | 2 | yes | S7006-ND | 1X08 | RFM-69 pins | PIN HEADER | Female pin header |  | https://www.digikey.com/product-detail/en/sullins-connector-solutions/PPTC081LFBN-RC/S7006-ND/810147
2 | PINHD-1X10 | Voltage Converter | 2 | 2 | 2 | 0 | 0 | yes | S7008-ND | 1X10 | Logic convertor Pins | PIN HEADER | Female pin header |  | https://www.digikey.com/product-detail/en/sullins-connector-solutions/PPTC101LFBN-RC/S7008-ND/810149
2 | PINHD-1X12 | SAMD21 | 2 | 2 | 2 | 2 | 2 | yes | S6100-ND | 1X12 | SAMD 21 pins | PIN HEADER | Female pin header |  | https://www.digikey.com/product-detail/en/sullins-connector-solutions/PPTC121LFBN-RC/S6100-ND/807231
5 | R-US_R1206 | 10k ohms | 1 | 4 | 1 | 4 | 1 | yes | RMCF1206JT10K0CT-ND (https://www.digikey.com/product-detail/en/stackpole-electronics-inc/RMCF1206JT10K0/RMCF1206JT10K0CT-ND/1942803) | R1206 | R12, R15, R16 | RESISTOR, American symbol |  |  | https://www.digikey.com/product-detail/en/stackpole-electronics-inc/RMCF1206JT10K0/RMCF1206JT10K0CT-ND/1942803
1 | R-US_R1206 | 120 ohms | 1 | 0 | 1 | 0 | 1 | yes | A129547CT-ND (https://www.digikey.com/product-detail/en/te-connectivity-passive-product/CRGH1206F120R/A129547CT-ND/8566751) | R1206 | R10 | RESISTOR, American symbol |  |  | https://www.digikey.com/product-detail/en/te-connectivity-passive-product/CRGH1206F120R/A129547CT-ND/8566751
7 | R-US_R1206 | 1K ohms | 1 | 0 | 1 | 0 | 1 | yes | RNCP1206FTD1K00CT-ND (https://www.digikey.com/product-detail/en/stackpole-electronics-inc/RNCP1206FTD1K00/RNCP1206FTD1K00CT-ND/2240675) | R1206 | R5, R6, R13, R18, R19 | RESISTOR, American symbol |  |  | https://www.digikey.com/product-detail/en/stackpole-electronics-inc/RNCP1206FTD1K00/RNCP1206FTD1K00CT-ND/2240675
1 | R-US_R1206 | 20K ohms | 1 | 0 | 1 | 0 | 1 | yes | RNCP1206FTD20K0CT-ND (https://www.digikey.com/product-detail/en/stackpole-electronics-inc/RNCP1206FTD20K0/RNCP1206FTD20K0CT-ND/2240718) | R1206 | R14 | RESISTOR, American symbol |  |  | https://www.digikey.com/product-detail/en/stackpole-electronics-inc/RNCP1206FTD20K0/RNCP1206FTD20K0CT-ND/2240718
1 | CONN_03-SCREW-5MM | CANBUS | 1 | 0 | 1 | 0 | 1 | yes | 732-2031-ND (https://www.digikey.com/product-detail/en/wurth-electronics-inc/691111710003/732-2031-ND/2060527) | SCREWTERMINAL-5MM-3 | CAN_HEADER | Multi connection point. Often used as Generic Header-pin footprint for 0.1 inch spaced/style header connections |  |  | https://www.digikey.com/product-detail/en/wurth-electronics-inc/691111710003/732-2031-ND/2060527 |  |  |  |  |  |  |  | CONN-10134 | PRT-08433
1 | JACK-PLUG0 | Power | 1 | 1 | 1 | 1 | 1 | yes | CP-031D-ND | DC power jack | BATT Power Jack |  | Input for DC voltage |  | https://www.digikey.com/products/en?keywords=CP-031D-ND
1 | R-78E-1.0 | 3.3V 1A RAIL | 1 | 1 | 1 | 1 | 1 | yes | 945-2409-5-ND | TUBE | 3.3V-REG | Provides a 3.3v @ 1A rail for all the components on the board |  |  | https://www.digikey.com/products/en?keywords=945-2409-5-ND
1 | R-78E5.0-1.0 | 5V 1A RAIL | 1 | 1 | 1 | 0 | 0 | yes | 945-2201-ND | TUBE | 5V-REG | Provides a 5v @ 1A rail for all the components on the board |  |  | https://www.digikey.com/products/en?keywords=945-2201-ND
 |  | Capcitors
Qty | Device Name | Value |  |  |  |  |  | In BoM? | Digikey Part Number | Package | Part Label | Description | DESCRIPTION | External Link | DIGI-KEY_PURCHASE_URL | MANUFACTURER_PART_NUMBER | MF | MP | MPN | OC_FARNELL | OC_NEWARK | PACKAGE | PROD_ID | SF_SKU | SPICEPREFIX | VALUE | VENDOR
2 | CAP-PTH | 33pF |  |  |  |  |  | yes | C410C330K3G5TA7200-ND | Axial | C8, C7 | CAPACITOR, American symbol | ceramic capcitors, smaller and have no polarity, can installed in any directions |  | https://www.digikey.com/products/en?keywords=C410C330K3G5TA7200-ND
2 | CAP-PTH | 0.1uF | 8 | 4 | 9 | 3 | 8 | yes | C430C104K3G5TA7200-ND | Axial | C5,C9 | CAPACITOR, American symbol | ceramic capcitors, smaller and have no polarity, can installed in any directions |  | https://www.digikey.com/products/en?keywords=C430C104K3G5TA7200-ND
5 | CAP-PTH | 10uF |  |  |  |  |  | yes | C430C106M3R5TA7200-ND | Axial | C4,C6,C2,C3,C1 | CAPACITOR, American symbol | ceramic capcitors, smaller and have no polarity, can installed in any directions |  | https://www.digikey.com/products/en?keywords=C430C106M3R5TA7200-ND
 |  | Surface mounted Devices
Qty | Device Name | Value |  |  |  |  |  | In BoM? | Digikey Part Number | Package | Part Label | Description | DESCRIPTION | External Link | DIGI-KEY_PURCHASE_URL | MANUFACTURER_PART_NUMBER | MF | MP | MPN | OC_FARNELL | OC_NEWARK | PACKAGE | PROD_ID | SF_SKU | SPICEPREFIX | VALUE | VENDOR
1 | 16MHz crystal | 16MHz | 1 | 0 | 1 | 0 | 1 | yes | XC1759-ND | XTAL_ECS-160-20-46X | Q1 | QUARTZ CRYSTAL T/H | Crystal 16MHz ¬±30ppm _Tol_ ¬±50ppm _Stability_ 20pF FUND 50Ohm |  | https://www.digikey.com/products/en?keywords=XC1759-ND |  | ECS Inc. | ECS-160-20-46X |  |  |  | HC46/X ECS International |  |  | B
1 | MCP2515(MCP2510)P | MCP2515 | 1 | 0 | 1 | 0 | 1 | yes | MCP2515-I/P-ND | DIP18 | IC1_2515 | CAN controller with SPI interface |  |  | https://www.digikey.com/products/en?keywords=MCP2515-I%2FP-ND |  |  |  |  |  |  |  | NA-XXXXX |  | X | MCP2515
1 | MCP2551DIL08 | MCP2551DIL08 | 1 | 0 | 1 | 0 | 1 | Yes | MCP2551-E/P-ND‎ | IC-PACKAGE_DIL08 | IC2_2551 | CAN transceiver |  |  | https://www.digikey.com/products/en?keywords=MCP2551-E%2FP-ND%E2%80%8E |  |  |  |  |  |  |  |  |  | X
1 | SAMD21 | 32 bit mircocontroller | 1 | 1 | 1 | 1 | 1 | yes |  | BREAKOUT |  |  | Main Microcontroller for the hole board | https://www.sparkfun.com/products/13664
1 | RFM69 BREAKOUT | RFM69HCW | 0 | 0 | 0 | 1 | 1 | yes |  | BREAKOUT | WRL-12775 |  | Long range COM link | https://www.sparkfun.com/products/12775
1 | SMA connector | 5-1814832-1 | 0 | 0 | 0 | 1 | 1 |  | A97594-ND |  |  | CONN SMA JACK STR 50 OHM PCB |  |  | https://www.digikey.com/product-detail/en/te-connectivity-amp-connectors/5-1814832-1/A97594-ND/1755982 | 5-1814832-1‎
1 | DX6 Reciever |  | 1 | 0 | 0 | 0 | 0 | yes |  | Module |  | SPEKTUM DX6 REMOTE CONTROLER RECIEVER |  | https://spektrumrc.com/Products/Default.aspx?ProdId=SPM6700
1 | TXB0108 ? Or CJMCU ? | 8-channel Bi-directional Logic Level Converter | 1 | ? | ? | ? | ? | yes |  | BREAKOUT |  | Logic shifter for BLUEthooth module and RF module |  | https://www.adafruit.com/product/395
1 | HC-0S | BLUETOOTH MODULE | 0 | 1 | 1 | 0 | 0 | yes |  | BREAKOUT |  | Bluetooth module for the board |  | https://www.amazon.com/Wireless-Bluetooth-Receiver-Transceiver-Transmitter/dp/B01MQKX7VP?hvadid=167146065113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
2 | 2 axis Joystick |  | 0 | 2 | 0 | 2 | 0 | yes |  | BREAKOUT | 245 | input joy stick for the remote control |  | https://www.adafruit.com/product/245
4 | SPST | Illuminated LED Duckbill Toggle Switch | 0 | 4 | 0 | 4 | 0 | yes |  |  | 76900 | SWITCHES FOR CONTROLING BOARD AND TRIKE |  | https://www.delcity.net/store/LED-Duckbill-Toggle-Switches/p_791291.h_791305
1 | Project box | BOX ABS GRAY 6.58"L X 4.21"W | 0 | 1 | 0 | 1 | 0 |  | HM225-ND |  |  |  |  |  | https://www.digikey.com/product-detail/en/hammond-manufacturing/1594ESGY/HM225-ND/153031

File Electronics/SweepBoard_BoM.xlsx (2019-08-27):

 |  | Through hole components
Qty | Device Name | Value | In BoM? | Digikey Part Number | Package | Part Label | Description | DESCRIPTION | External Link | DIGI-KEY_PURCHASE_URL | MANUFACTURER_PART_NUMBER | MF | MP | MPN | OC_FARNELL | OC_NEWARK | PACKAGE | PROD_ID | SF_SKU | SPICEPREFIX | VALUE | VENDOR
2 | PINHD-1X2 |  | yes | 732-5315-ND | 1X02 | 5V TEST,CAN_SS test | PIN HEADER
2 | PINHD-1X6 |  | yes | S5481-ND | 1X06 | HC-05 BLUETOOTH | PIN HEADER | Right Angle Female PIN Header
1 | Can Plug |  | Yes | 277-1579-ND | SCREWTERMINAL-5MM-4 | CAN_HEADER | 4 Position Wire to Board Terminal Block Horizontal with Board 0.197" (5.00mm) Through Hole |  |  | https://www.digikey.com/product-detail/en/phoenix-contact/1935187/277-1579-ND/568616
1 | R-US_R1206 | 10k ohms | yes | RMCF1206JT10K0CT-ND (https://www.digikey.com/product-detail/en/stackpole-electronics-inc/RMCF1206JT10K0/RMCF1206JT10K0CT-ND/1942803) | R1206 | R12, R15, R16 | RESISTOR, American symbol
1 | R-US_R1206 | 120 ohms | yes | A129547CT-ND (https://www.digikey.com/product-detail/en/te-connectivity-passive-product/CRGH1206F120R/A129547CT-ND/8566751) | R1206 | R10 | RESISTOR, American symbol
1 | R-US_R1206 | 1K ohms | yes | RNCP1206FTD1K00CT-ND (https://www.digikey.com/product-detail/en/stackpole-electronics-inc/RNCP1206FTD1K00/RNCP1206FTD1K00CT-ND/2240675) | R1206 | R5, R6, R13, R18, R19 | RESISTOR, American symbol
1 | R-US_R1206 | 20K ohms | yes | RNCP1206FTD20K0CT-ND (https://www.digikey.com/product-detail/en/stackpole-electronics-inc/RNCP1206FTD20K0/RNCP1206FTD20K0CT-ND/2240718) | R1206 | R14 | RESISTOR, American symbol
1 | R-78E5.0-1.0 | 5V 1A RAIL | yes | 945-2201-ND | TUBE | 5V-REG | Provides a 5v @ 1A rail for all the components on the board
 |  | Capcitors
Qty | Device Name | Value | In BoM? | Digikey Part Number | Package | Part Label | Description | DESCRIPTION | External Link | DIGI-KEY_PURCHASE_URL | MANUFACTURER_PART_NUMBER | MF | MP | MPN | OC_FARNELL | OC_NEWARK | PACKAGE | PROD_ID | SF_SKU | SPICEPREFIX | VALUE | VENDOR
7 | CAP | 0.1uF | yes | C430C104K3G5TA7200-ND | Axial | C5,C9 | CAPACITOR, American symbol | ceramic capcitors, smaller and have no polarity, can installed in any directions
 |  | Surface mounted Devices
Qty | Device Name | Value | In BoM? | Digikey Part Number | Package | Part Label | Description | DESCRIPTION | External Link | DIGI-KEY_PURCHASE_URL | MANUFACTURER_PART_NUMBER | MF | MP | MPN | OC_FARNELL | OC_NEWARK | PACKAGE | PROD_ID | SF_SKU | SPICEPREFIX | VALUE | VENDOR
1 | 16MHz crystal | 16MHz | yes | XC1759-ND | XTAL_ECS-160-20-46X | Q1 | QUARTZ CRYSTAL T/H | Crystal 16MHz ¬±30ppm _Tol_ ¬±50ppm _Stability_ 20pF FUND 50Ohm | XC1759-ND | https://www.digikey.com/product-detail/en/ecs-inc/ECS-160-20-46X/XC1759-ND/2676589 |  | ECS Inc. | ECS-160-20-46X |  |  |  | HC46/X ECS International |  |  | B
1 | MCP2515(MCP2510)P | MCP2515 | yes | MCP2515-I/P-ND | DIP18 | IC1_2515 | CAN controller with SPI interface |  |  |  |  |  |  |  |  |  |  | NA-XXXXX |  | X | MCP2515
1 | MCP2551DIL08 | MCP2551DIL08 | Yes | MCP2551-E/P-ND‎ | IC-PACKAGE_DIL08 | IC2_2551 | CAN transceiver |  |  |  |  |  |  |  |  |  |  |  |  | X
1 | Arduino Micro |  | yes |  |  |  |  |  | https://store.arduino.cc/usa/arduino-micro

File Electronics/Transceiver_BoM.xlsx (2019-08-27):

 |  | Board Manufacturer Specs
 | Traces are 15 mil | Board needs 2 oz copper |  | Two Layers: Front & Back
 |  | Through hole components
Qty | Device Name | Value | In BoM? | Digikey Part Number | Package | Part Label | Description | DESCRIPTION | External Link | DIGI-KEY_PURCHASE_URL | MANUFACTURER_PART_NUMBER | MF | MP | MPN | OC_FARNELL | OC_NEWARK | PACKAGE | PROD_ID | SF_SKU | SPICEPREFIX | VALUE | VENDOR
5 | PINHD-1X2 |  | yes | 732-5315-ND | 1X02 | 5V TEST,3.3V TEST, JUMPER, RADIO-OK | PIN HEADER
5 | PINHD-1X3 |  | yes | 732-5316-ND | 1X03 | REST SW,POWER SW,AUTO MNL,ESTOP,REVERSE | PIN HEADER
2 | PINHD-1X4 |  | yes | 732-5317-ND | 1X04 | LEFT JOY STICK, RIGHT JOYSTICK | PIN HEADER
2 | PINHD-1X6 |  | yes | S5481-ND | 1X06 | HC-05 BLUETOOTH | PIN HEADER | Right Angle Female PIN Header
3 | PINHD-1X7 |  | yes | S7040-ND | 1X07 | RC-RECEIVER | PIN HEADER | Female pin header
2 | PINHD-1X8 |  | yes | S7006-ND | 1X08 | RFM-69 pins | PIN HEADER | Female pin header
2 | PINHD-1X10 |  | yes | S7008-ND | 1X10 | Logic convertor Pins | PIN HEADER | Female pin header
2 | PINHD-1X12 |  | yes | S6100-ND | 1X12 | SAMD 21 pins | PIN HEADER | Female pin header
5 | R-US_R1206 | 10k ohms | yes | RMCF1206JT10K0CT-ND (https://www.digikey.com/product-detail/en/stackpole-electronics-inc/RMCF1206JT10K0/RMCF1206JT10K0CT-ND/1942803) | R1206 | R12, R15, R16 | RESISTOR, American symbol
1 | R-US_R1206 | 120 ohms | yes | A129547CT-ND (https://www.digikey.com/product-detail/en/te-connectivity-passive-product/CRGH1206F120R/A129547CT-ND/8566751) | R1206 | R10 | RESISTOR, American symbol
7 | R-US_R1206 | 1K ohms | yes | RNCP1206FTD1K00CT-ND (https://www.digikey.com/product-detail/en/stackpole-electronics-inc/RNCP1206FTD1K00/RNCP1206FTD1K00CT-ND/2240675) | R1206 | R5, R6, R13, R18, R19 | RESISTOR, American symbol
1 | R-US_R1206 | 20K ohms | yes | RNCP1206FTD20K0CT-ND (https://www.digikey.com/product-detail/en/stackpole-electronics-inc/RNCP1206FTD20K0/RNCP1206FTD20K0CT-ND/2240718) | R1206 | R14 | RESISTOR, American symbol
1 | CONN_03-SCREW-5MM |  | yes | 732-2031-ND (https://www.digikey.com/product-detail/en/wurth-electronics-inc/691111710003/732-2031-ND/2060527) | SCREWTERMINAL-5MM-3 | CAN_HEADER | Multi connection point. Often used as Generic Header-pin footprint for 0.1 inch spaced/style header connections |  |  |  |  |  |  |  |  |  |  | CONN-10134 | PRT-08433
1 | JACK-PLUG0 |  | yes | CP-031D-ND | DC power jack | BATT Power Jack |  | Input for DC voltage
1 | R-78E-1.0 | 3.3V 1 A RAIL | yes | 945-2409-5-ND | TUBE | 3.3V-REG | Provides a 3.3v @ 1A rail for all the components on the board
1 | R-78E5.0-1.0 | 5V 1A RAIL | yes | 945-2201-ND | TUBE | 5V-REG | Provides a 5v @ 1A rail for all the components on the board
 |  | Capcitors
Qty | Device Name | Value | In BoM? | Digikey Part Number | Package | Part Label | Description | DESCRIPTION | External Link | DIGI-KEY_PURCHASE_URL | MANUFACTURER_PART_NUMBER | MF | MP | MPN | OC_FARNELL | OC_NEWARK | PACKAGE | PROD_ID | SF_SKU | SPICEPREFIX | VALUE | VENDOR
2 | CAP-PTH | 33pF | yes | C410C330K3G5TA7200-ND | Axial | C8, C7 | CAPACITOR, American symbol | ceramic capcitors, smaller and have no polarity, can installed in any directions |  | https://www.digikey.com/products/en/capacitors/ceramic-capacitors/60?k=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
2 | CAP-PTH | 0.1uF | yes | C430C104K3G5TA7200-ND | Axial | C5,C9 | CAPACITOR, American symbol | ceramic capcitors, smaller and have no polarity, can installed in any directions
5 | CAP-PTH | 10uF | yes | C430C106M3R5TA7200-ND | Axial | C4,C6,C2,C3,C1 | CAPACITOR, American symbol | ceramic capcitors, smaller and have no polarity, can installed in any directions
 |  | Surface mounted Devices
Qty | Device Name | Value | In BoM? | Digikey Part Number | Package | Part Label | Description | DESCRIPTION | External Link | DIGI-KEY_PURCHASE_URL | MANUFACTURER_PART_NUMBER | MF | MP | MPN | OC_FARNELL | OC_NEWARK | PACKAGE | PROD_ID | SF_SKU | SPICEPREFIX | VALUE | VENDOR
1 | 16MHz crystal | 16MHz | yes | XC1759-ND | XTAL_ECS-160-20-46X | Q1 | QUARTZ CRYSTAL T/H | Crystal 16MHz ¬±30ppm _Tol_ ¬±50ppm _Stability_ 20pF FUND 50Ohm | XC1759-ND | https://www.digikey.com/product-detail/en/ecs-inc/ECS-160-20-46X/XC1759-ND/2676589 |  | ECS Inc. | ECS-160-20-46X |  |  |  | HC46/X ECS International |  |  | B
1 | MCP2515(MCP2510)P | MCP2515 | yes | MCP2515-I/P-ND | DIP18 | IC1_2515 | CAN controller with SPI interface |  |  |  |  |  |  |  |  |  |  | NA-XXXXX |  | X | MCP2515
1 | MCP2551DIL08 | MCP2551DIL08 | Yes | MCP2551-E/P-ND‎ | IC-PACKAGE_DIL08 | IC2_2551 | CAN transceiver |  |  |  |  |  |  |  |  |  |  |  |  | X
1 | SAMD21 | 32 bit mircocontroller | yes |  | BREAKOUT |  |  | Main Microcontroller for the hole board | https://www.sparkfun.com/products/13664
1 | RFM69 BREAKOUT | RFM69HCW | yes |  | BREAKOUT | WRL-12775 |  | Long range COM link | https://www.sparkfun.com/products/12775
1 | DX6 Reciever |  | yes |  | Module |  | SPEKTUM DX6 REMOTE CONTROLER RECIEVER |  | https://spektrumrc.com/Products/Default.aspx?ProdId=SPM6700
1 | TXB0108 | 8-channel Bi-directional Logic Level Converter | yes |  | BREAKOUT |  | Logic shifter for BLUEthooth module and RF module |  | https://www.adafruit.com/product/395
1 | HC-0S | BLUETOOTH MODULE | yes |  | BREAKOUT |  | Bluetooth module for the board |  | https://www.amazon.com/Wireless-Bluetooth-Receiver-Transceiver-Transmitter/dp/B01MQKX7VP?hvadid=167146065113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
2 | 2 axis Joystick |  | yes |  | BREAKOUT | 245 | input joy stick for the remote control |  | https://www.adafruit.com/product/245
5 | SPST | Illuminated LED Duckbill Toggle Switch | yes |  |  | 76900 | SWITCHES FOR CONTROLING BOARD AND TRIKE |  | https://www.delcity.net/store/LED-Duckbill-Toggle-Switches/p_791291.h_791305

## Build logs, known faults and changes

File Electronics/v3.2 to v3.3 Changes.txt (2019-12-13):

Changes from 3.2 to next version 3.3:

MCP 2510 cut and  jumped so that power supply pin is 3.3v, not 5v.
MCP 2551 does not need a 5v supply. Rcv Radio version will need a 5v rail.
4 screw pin terminal to CAN.
Update capacitor values on schematic and txt. 
Position capacitors closer to their target components.
Make power and ground lines thicker, add ground plane if possible.
Sesies resistor for LED: 1K.
R9 is grounded on both ends, fix.
GRND renamed properly as slope control. 
Sync .BRD and .SCH files.

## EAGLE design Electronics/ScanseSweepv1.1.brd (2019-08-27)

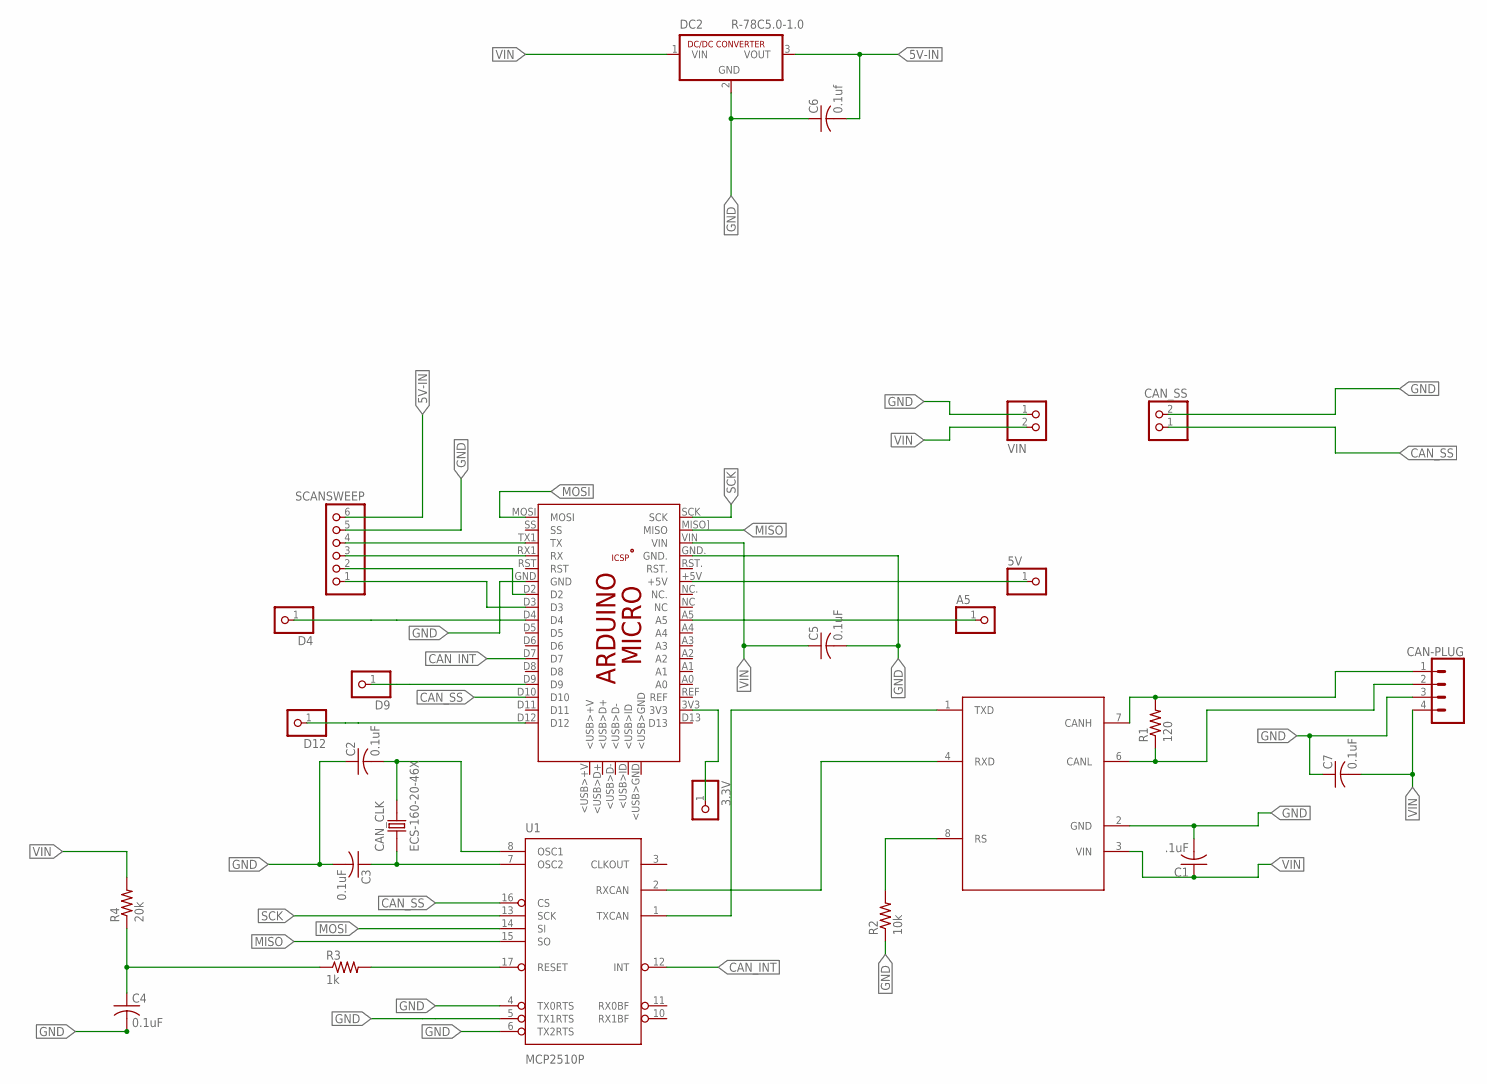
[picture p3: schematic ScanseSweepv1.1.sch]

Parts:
3.3V, 5V: PINHD-1X1; 1X01
A5: PINHD-1X1; 1X01
C1: .1uF; C025-024X044
C2, C3, C4, C5, C7: 0.1uF; C025-024X044
C6: 0.1uf; C025-024X044
CAN_CLK: ECS-160-20-46X; XTAL_ECS-160-20-46X
CAN_SS_TEST: CAN_SS; 1X02
D4, D9, D12: PINHD-1X1; 1X01
DC2: R-78C5.0-1.0; SIP3
J1: CAN-PLUG; SCREWTERMINAL-3.5MM-4
PCB1: ARDUINO_MICRO
R1: 120; 0204/5
R2: 10k; 0204/5
R3: 1k; 0204/5
R4: 20k; 0204/5
SCANSESWEEP: SCANSWEEP; 1X06
U1: MCP2510P; DIL18
U$1: MCP2551MCP2551; DIL08
VIN_TEST: VIN; 1X02

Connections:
3.3V: 3.3V.1, PCB1.3V3
5V: 5V.1, PCB1.+5V
5V-IN: C6.2, DC2.3 (VOUT), SCANSESWEEP.6
A5: A5.1, PCB1.A5
CANH: J1.1, R1.2, U$1.7 (CANH)
CANL: J1.2, R1.1, U$1.6 (CANL)
CAN_INT: PCB1.D7, U1.12 (INT)
CAN_SS: CAN_SS_TEST.1, PCB1.D10, U1.16 (CS)
D2: PCB1.D2, SCANSESWEEP.2
D3: PCB1.D3, SCANSESWEEP.1
D4: D4.1, PCB1.D4
D9: D9.1, PCB1.D9
D12: D12.1, PCB1.D12
GND: C1.2, C2.1, C3.2, C4.2, C5.2, C6.1, C7.1, CAN_SS_TEST.2, DC2.2 (GND), J1.3, PCB1.GND, PCB1.GND., R2.1, SCANSESWEEP.5, U1.4 (TX0RTS), U1.5 (TX1RTS), U1.6 (TX2RTS), U$1.2 (GND), VIN_TEST.1
MISO: PCB1.MISO] (MISO), U1.15 (SO)
MOSI: PCB1.MOSI, U1.14 (SI)
unnamed: C4.1, R3.1, R4.1
OSC1: C2.2, CAN_CLK.2, U1.8 (OSC1)
OSC2: C3.1, CAN_CLK.1, U1.7 (OSC2)
RESET: R3.2, U1.17 (RESET)
RS: R2.2, U$1.8 (RS)
RX: PCB1.RX1 (RX), SCANSESWEEP.3
RXCAN: U1.2 (RXCAN), U$1.4 (RXD)
SCK: PCB1.SCK, U1.13 (SCK)
TX: PCB1.TX1 (TX), SCANSESWEEP.4
TXCAN: U1.1 (TXCAN), U$1.1 (TXD)
VIN: C1.1, C5.1, C7.2, DC2.1 (VIN), J1.4, PCB1.VIN, R4.2, U$1.3 (VIN), VIN_TEST.2

Board: 2 copper layers, 26 parts (0 on the bottom side), 27 nets, no tracks yet.

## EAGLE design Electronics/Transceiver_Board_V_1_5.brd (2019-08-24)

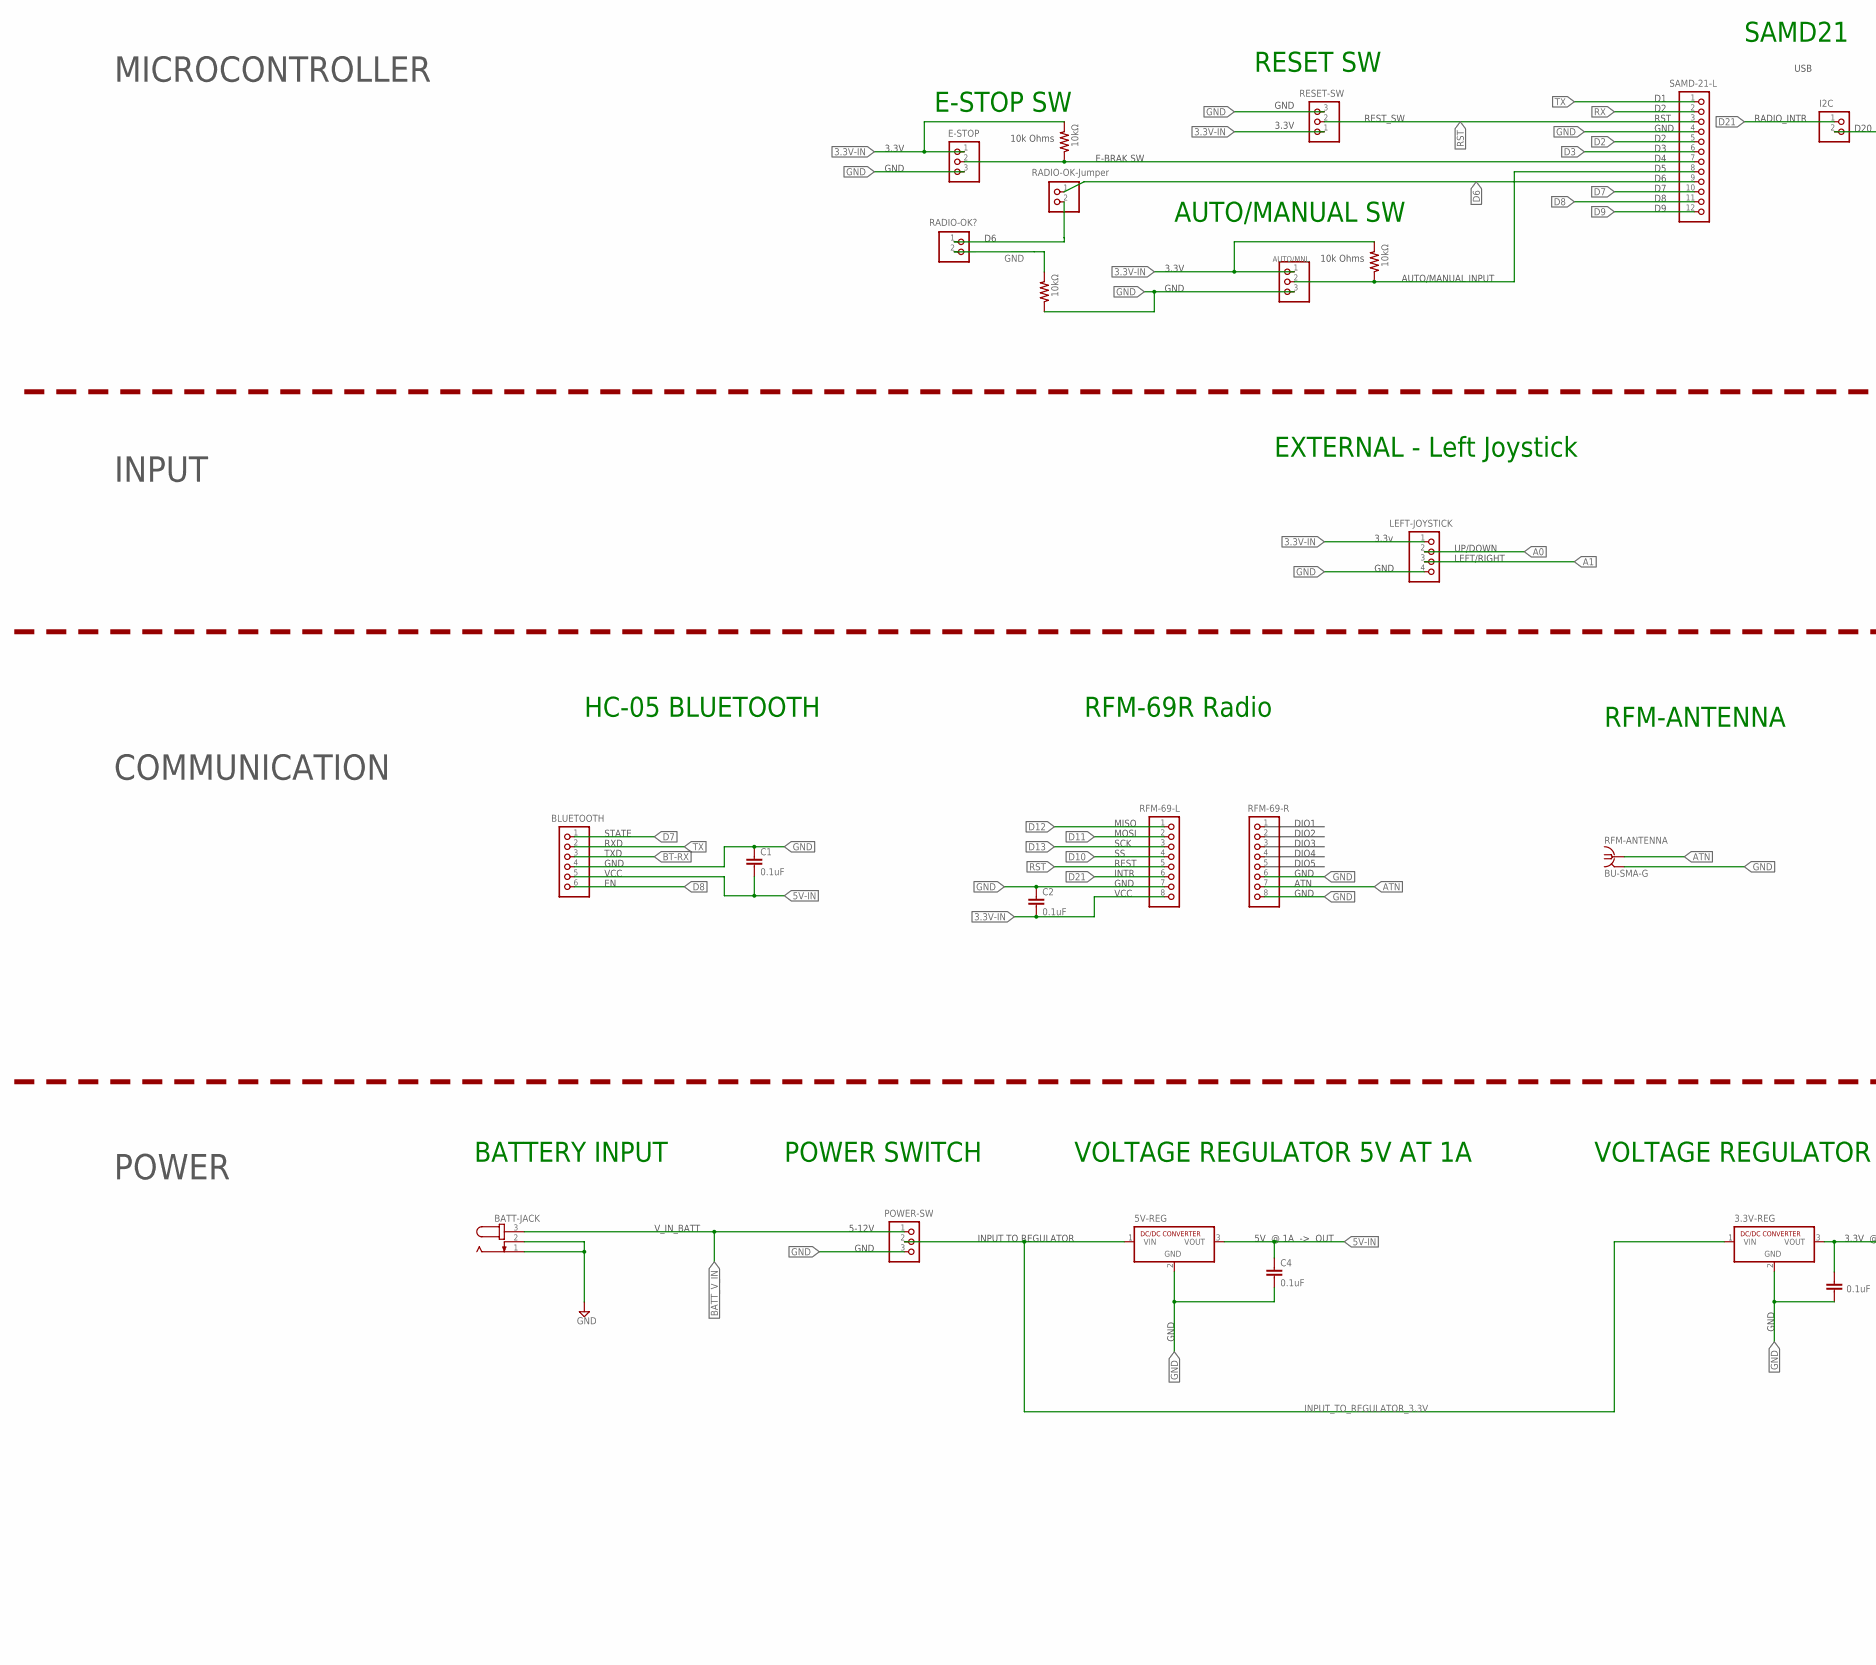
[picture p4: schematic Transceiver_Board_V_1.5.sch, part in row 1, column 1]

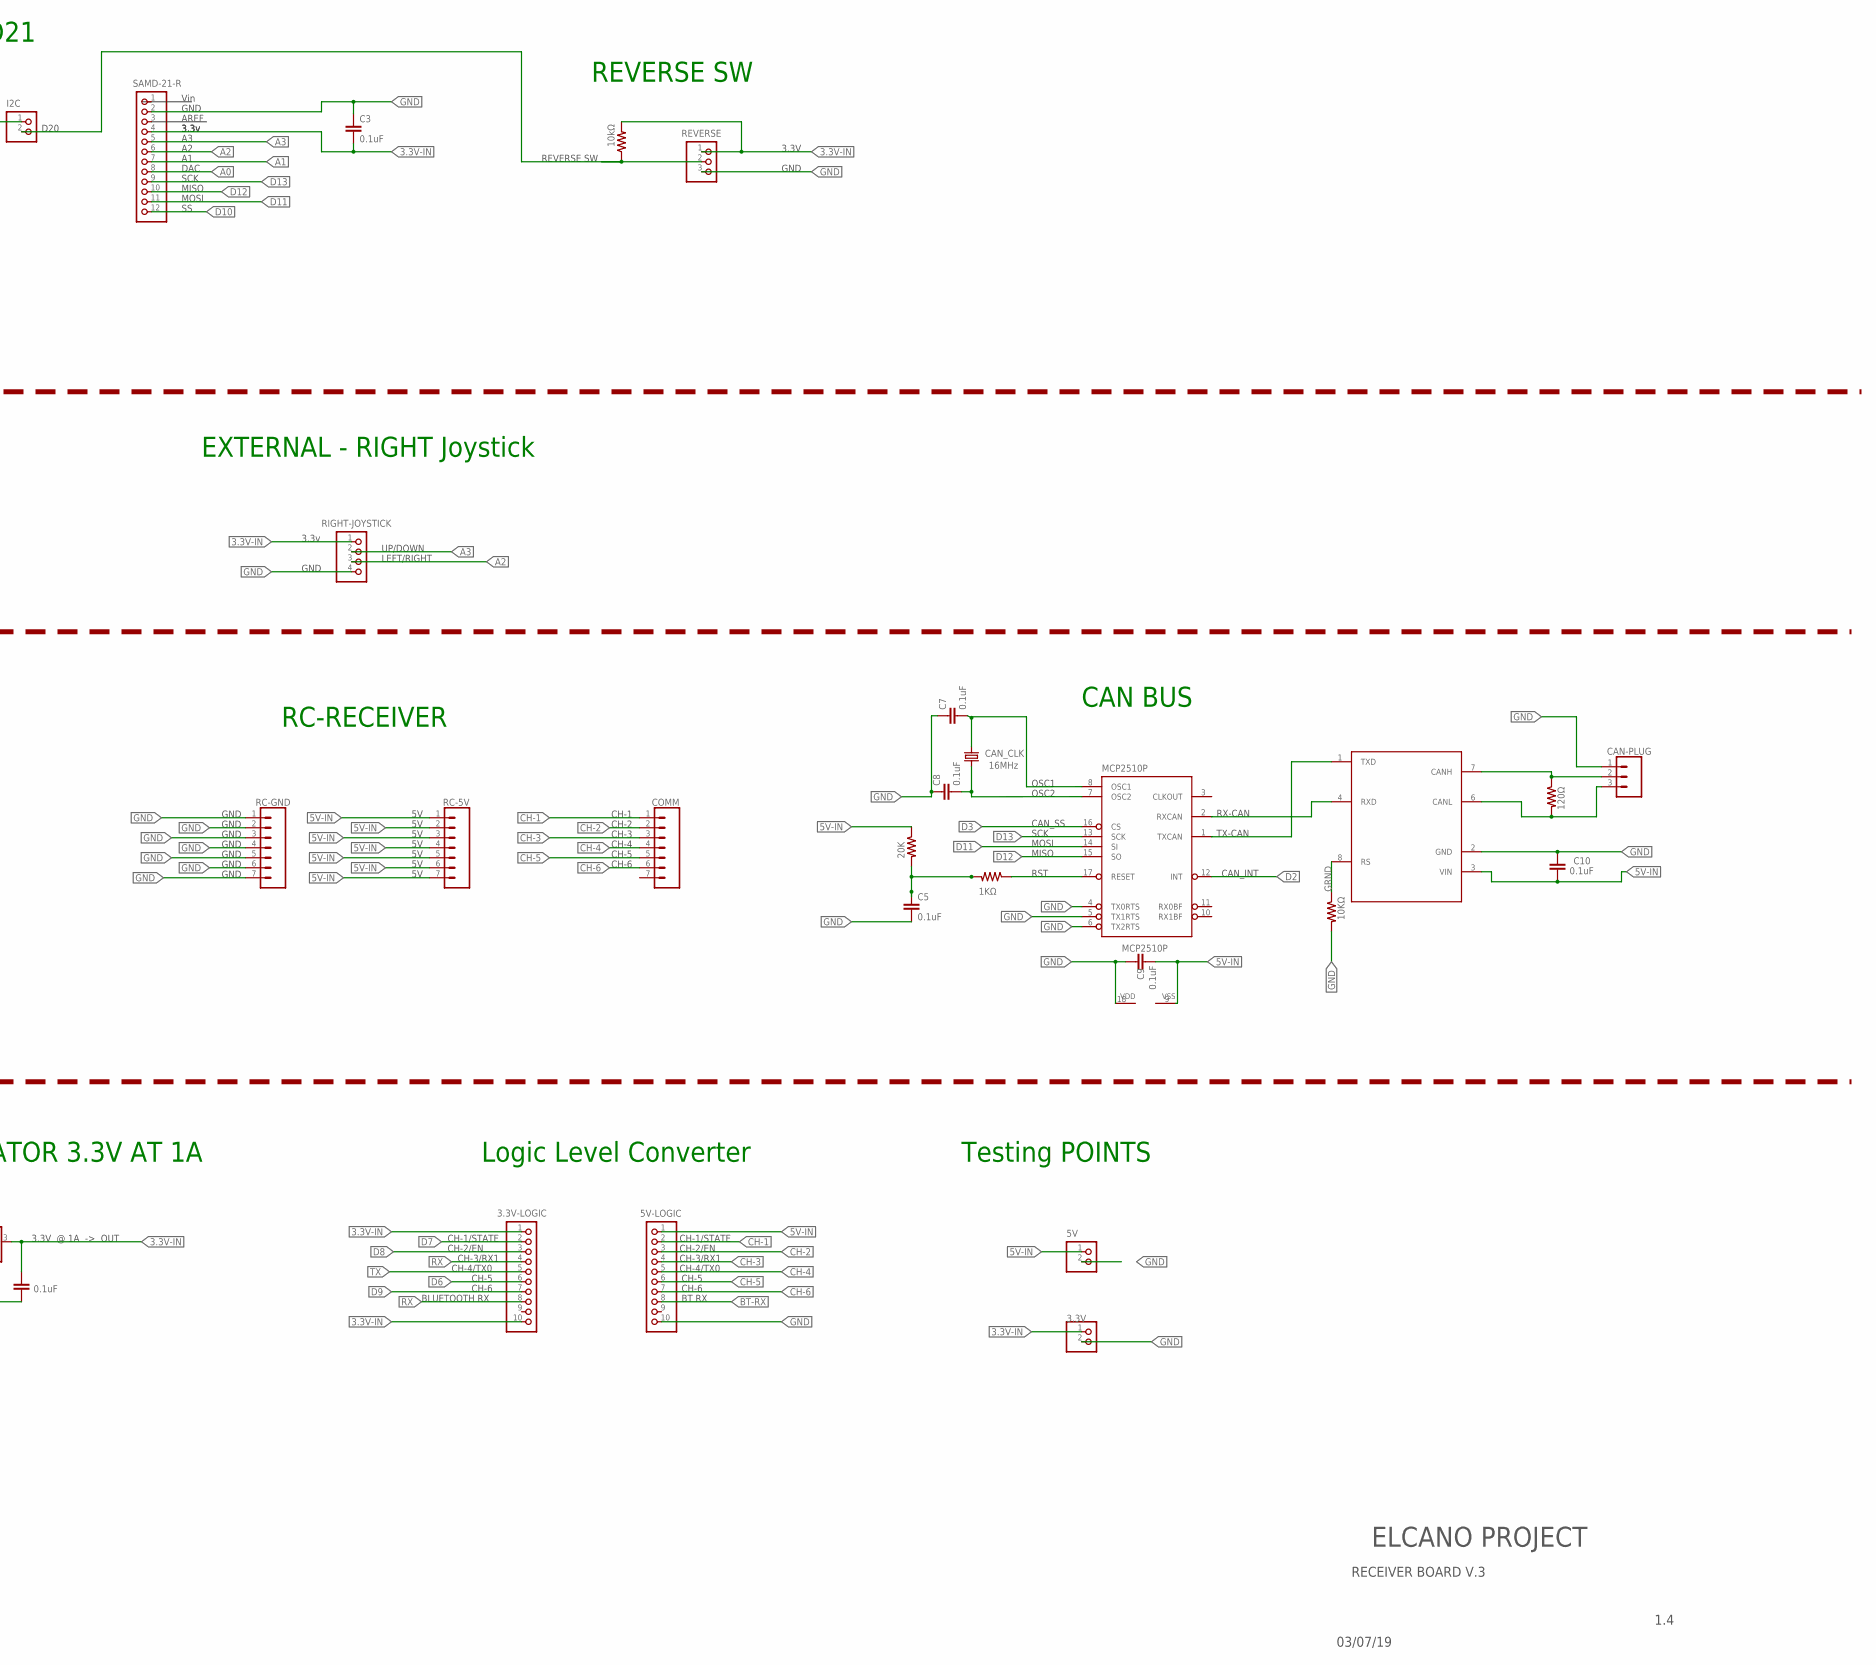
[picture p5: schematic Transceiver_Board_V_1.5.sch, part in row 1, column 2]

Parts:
3.3-LOGIC: 3.3V-LOGIC; 1X10
3.3V-REG: 3.3V REG; SIP3
3.3V-TEST: 3.3V; 1X02
5V-LOGIC: 5V-LOGIC; 1X10
5V-REG: 5V REG; SIP3
5V-TEST: 5V; 1X02
AT/M: AUTO/MNL; 1X03
BATTERY_INPUT_JACK: BATT-JACK; SPC4077
BLUETOOTH: BLUETOOTH; 1X06
C1, C2, C3, C4, C5, C6, C7, C8, C9, C10: 0.1uF; CAP-PTH-SMALL-KIT
CAN_CLK: 16MHz; HC49US
CAN_PLUG: CAN-PLUG; SCREWTERMINAL-5MM-3
COMM: COMM; 1X07
E-STOP: E-STOP; 1X03
I2C: I2C; 1X02
JOY-STICK-L: LEFT-JOYSTICK; 1X04
JOY-STICK-R: RIGHT-JOYSTICK; 1X04
MCP2510P: MCP2510P; DIL18
MCP2551: MCP2551MCP2551; DIL08
POWER-SW: POWER-SW; 1X03
R1, R2, R3, R9: 10kΩ; 0204/7
R5: 1KΩ; 0204/7
R6: 20K; 0204/7
R7: 10KΩ; 0204/7
R8: 120Ω; 0204/7
RADIO-OK1: RADIO-OK-Jumper; 1X02
RADIO-OK?: RADIO-OK?; 1X02
RC-5V: RC-5V; 1X07
RC-GND: RC-GND; 1X07
RESET-SW: RESET-SW; 1X03
REVERSE: REVERSE; 1X03
RFM-69: RFM-69-R; 1X08
RFM-ANTENNA: BU-SMA-G
RFM_L: RFM-69-L; 1X08
SAMD-21_R: SAMD-21-R; 1X12
SAMD_21_L: SAMD-21-L; 1X12

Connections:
3.3V-IN: 3.3-LOGIC.1, 3.3-LOGIC.10, 3.3V-REG.3 (VOUT), 3.3V-TEST.1, AT/M.1, C2.2, C3.2, C6.1, E-STOP.1, JOY-STICK-L.1, JOY-STICK-R.1, R1.2, R2.2, R3.2, RESET-SW.1, REVERSE.1, RFM_L.8, SAMD-21_R.4
3.3V-IN1: C5.1, R5.2, R6.2
5V-IN: 5V-LOGIC.1, 5V-REG.3 (VOUT), 5V-TEST.1, BLUETOOTH.5, C1.2, C4.1, C9.2, C10.2, MCP2510P.9 (VSS), MCP2551.3 (VIN), R6.1, RC-5V.1, RC-5V.2, RC-5V.3, RC-5V.4, RC-5V.5, RC-5V.6, RC-5V.7
A0: JOY-STICK-L.2, SAMD-21_R.8
A1: JOY-STICK-L.3, SAMD-21_R.7
A2: JOY-STICK-R.3, SAMD-21_R.6
A3: JOY-STICK-R.2, SAMD-21_R.5
ATN: RFM-69.7, RFM-ANTENNA.1
BATT_V_IN: BATTERY_INPUT_JACK.3, POWER-SW.1
BT-RX: 5V-LOGIC.8, BLUETOOTH.3
CANH: CAN_PLUG.2, MCP2551.7 (CANH), R8.1
CANL: CAN_PLUG.3, MCP2551.6 (CANL), R8.2
CAN_RST: MCP2510P.17 (RESET), R5.1
CH-1: 5V-LOGIC.2, COMM.1
CH-2: 5V-LOGIC.3, COMM.2
CH-3: 5V-LOGIC.4, COMM.3
CH-4: 5V-LOGIC.5, COMM.4
CH-5: 5V-LOGIC.6, COMM.5
CH-6: 5V-LOGIC.7, COMM.6
D2: MCP2510P.12 (INT), SAMD_21_L.5
D3: MCP2510P.16 (CS), SAMD_21_L.6
D4: E-STOP.2, R1.1, SAMD_21_L.7
D5: AT/M.2, R2.1, SAMD_21_L.8
D6: 3.3-LOGIC.6, RADIO-OK1.1, SAMD_21_L.9
D7: 3.3-LOGIC.2, BLUETOOTH.1, SAMD_21_L.10
D8: 3.3-LOGIC.3, BLUETOOTH.6, SAMD_21_L.11
D9: 3.3-LOGIC.7, SAMD_21_L.12
D10: RFM_L.4, SAMD-21_R.12
D11: MCP2510P.14 (SI), RFM_L.2, SAMD-21_R.11
D12: MCP2510P.15 (SO), RFM_L.1, SAMD-21_R.10
D13: MCP2510P.13 (SCK), RFM_L.3, SAMD-21_R.9
D20: I2C.2, R3.1, REVERSE.2
D21: I2C.1, RFM_L.6
GND: 3.3V-REG.2 (GND), 3.3V-TEST.2, 5V-LOGIC.10, 5V-REG.2 (GND), 5V-TEST.2, AT/M.3, BATTERY_INPUT_JACK.1, BATTERY_INPUT_JACK.2, BLUETOOTH.4, C1.1, C2.1, C3.1, C4.2, C5.2, C6.2, C7.1, C8.1, C9.1, C10.1, CAN_PLUG.1, E-STOP.3, JOY-STICK-L.4, JOY-STICK-R.4, MCP2510P.4 (TX0RTS), MCP2510P.5 (TX1RTS), MCP2510P.6 (TX2RTS), MCP2510P.18 (VDD), MCP2551.2 (GND), POWER-SW.3, R7.2, R9.1, R9.2, RADIO-OK?.2, RC-GND.1, RC-GND.2, RC-GND.3, RC-GND.4, RC-GND.5, RC-GND.6, RC-GND.7, RESET-SW.3, REVERSE.3, RFM-69.6, RFM-69.8, RFM-ANTENNA.2, RFM-ANTENNA.3 (2), RFM-ANTENNA.4 (2), RFM-ANTENNA.5 (2), RFM_L.7, SAMD-21_R.2, SAMD_21_L.4
GRND: MCP2551.8 (RS), R7.1
INPUT_TO_REGULATOR_3.3V: 3.3V-REG.1 (VIN), 5V-REG.1 (VIN), POWER-SW.2
unnamed: RADIO-OK1.2, RADIO-OK?.1
OSC1: C7.2, CAN_CLK.1, MCP2510P.8 (OSC1)
OSC2: C8.2, CAN_CLK.2, MCP2510P.7 (OSC2)
RST: RESET-SW.2, RFM_L.5, SAMD_21_L.3
RX: 3.3-LOGIC.4, 3.3-LOGIC.8, SAMD_21_L.2
RX-CAN: MCP2510P.2 (RXCAN), MCP2551.4 (RXD)
TX: 3.3-LOGIC.5, BLUETOOTH.2, SAMD_21_L.1
TX-CAN: MCP2510P.1 (TXCAN), MCP2551.1 (TXD)

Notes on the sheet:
RST
GND
Vin
3.3v
DAC
SCK
MISO
MOSI
SAMD21
RFM-69R Radio
USB
RFM-ANTENNA
EXTERNAL - Left Joystick
DIO1
DIO2
DIO3
DIO4
DIO5
ATN
UP/DOWN
LEFT/RIGHT
EXTERNAL - RIGHT Joystick
STATE
RXD
TXD
VCC
HC-05 BLUETOOTH
E-BRAK SW
3.3V
AUTO/MANUAL INPUT
REVERSE SW
E-STOP SW
AUTO/MANUAL SW
REST_SW
RESET SW
VOLTAGE REGULATOR 5V AT 1A
BATTERY INPUT
VOLTAGE REGULATOR 3.3V AT 1A
REST
Testing POINTS

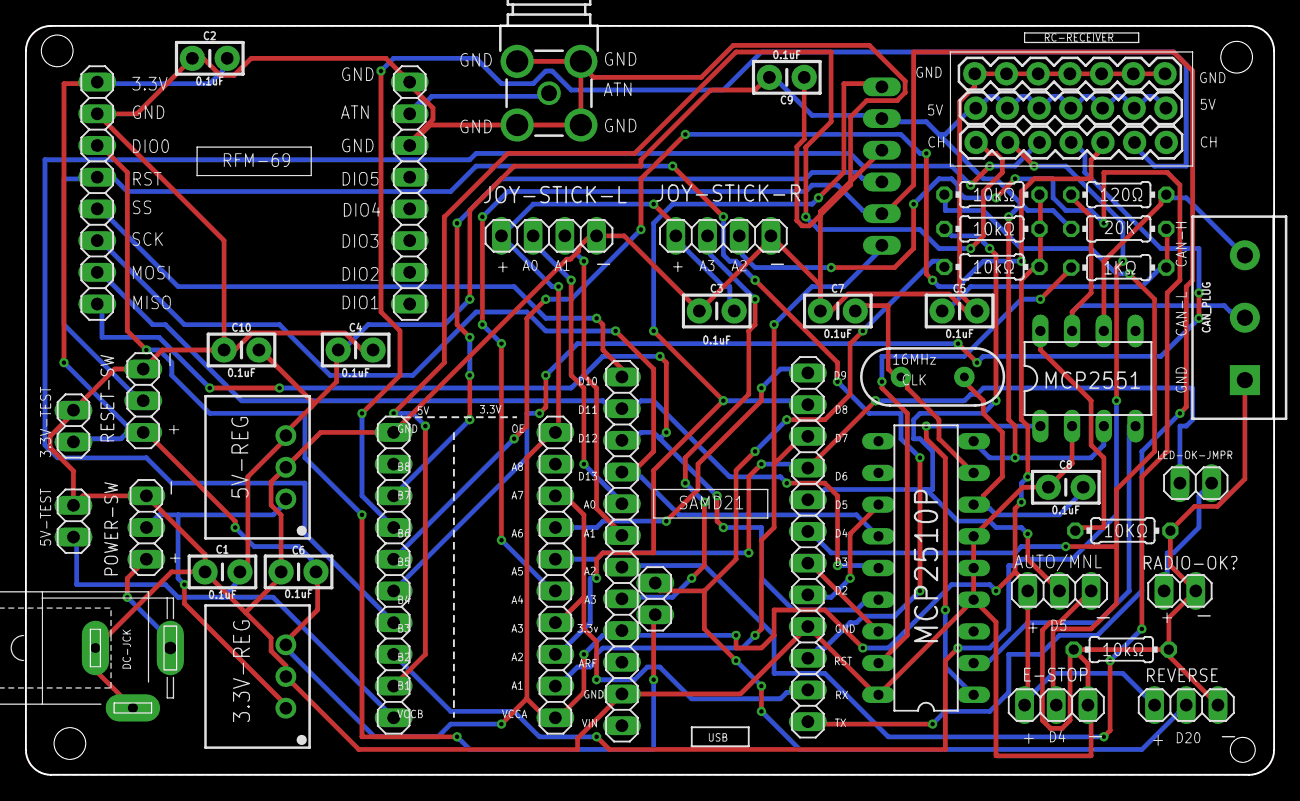
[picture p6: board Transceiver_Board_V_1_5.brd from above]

Board: 2 copper layers, 100.0 x 60.0 mm, 48 parts (1 on the bottom side), 44 nets.

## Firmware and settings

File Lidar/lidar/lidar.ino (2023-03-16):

/*
   Sweep Obstacle Detector
   by B. Johnson

   modified 5/8/2019 JB: removed code not required for testing lidar
    added angle limit functionality
    added scan segment functionality
    

   Runs on Arduino Micro connected to Scanse Sweep;
   For best results, Scanse Sweep should have a 400mA, 5V power source
   connect power, synch, tx, rx, and ground wires before beginning
   Serial1 (connection to Sweep) uses pins 0 and 1

   0 or 360 degrees aligns with the Sweep LED, so (x= -1, y= 0) or 180 degrees is straight forward
*/

/************************** LEO Added **********************/
// #include <mcp_can.h>      // <---- Import from another library: Seeed-Studio/CAN-BUS-Shield
// #include <mcp_can_dfs.h>  //       (install Library from Arduino, search for "Can-Bus-Shield")
#include <mcp2515_can.h>        // <---- Import from library: Seed-Studio/CAN-BUS-Shield
#include <mcp2515_can_dfs.h>    // <---- Import from library: Seed-Studio/CAN-BUS-Shield
#include <Can_Protocol.h> // <---- Import from path: elcano/Elcano_C2_LowLevel/Can_Protocol.h
/*************************** END *****************************/

#include <Sweep.h> // https://github.com/scanse/sweep-arduino/tree/master/Sweep

const uint8_t POWER_PIN = 2; // Power Enable pin
const uint8_t SYNC_PIN = 3;  // Sync / Device Ready pin

const uint32_t SERIAL_BAUD_RATE = 115200; // Baud rate for Serial. 14,400 bytes/s, 14.4 bytes/ms

const uint8_t MOTOR_SPEED_HZ = 1;                               // Number of rotations per second
const uint8_t (&MOTOR_SPEED_CODE)[2] = MOTOR_SPEED_CODE_1_HZ;   // Number of rotations per second
const uint16_t SAMPLE_RATE_HZ = 750;                            // Number of samples per second
const uint8_t (&SAMPLE_RATE_CODE)[2] = SAMPLE_RATE_CODE_750_HZ; // Number of samples per second

const uint8_t NOISE_FLOOR = 50;                                              // adjust this to filter garbage readings
const uint8_t NUM_FRACTIONAL_BITS = 4;                                       // Number of fractional bits in raw angle
const uint16_t RIGHT_ANGLE_BOUNDARY = 1;                                     // Right boundary angle of scan range
const uint16_t R_ANGLE_FIXEDP = RIGHT_ANGLE_BOUNDARY << NUM_FRACTIONAL_BITS; // use this to test "raw angle" value lower boundary
const uint16_t LEFT_ANGLE_BOUNDARY = 359;                                    // Left boundary angle of scan range
const uint16_t L_ANGLE_FIXEDP = LEFT_ANGLE_BOUNDARY << NUM_FRACTIONAL_BITS;  // use this to test "raw angle" value upper boundary

const uint16_t MAX_DELTA = 15; // max change per scan segment in cm; values greater than this will start a new segment

/*************************** LEO Added *************************/
// 8 bits = 1 byte
// uint16_t = unsigned int or int
// uint8_t = unsigned char or char
typedef union {
    struct
    {
        uint16_t range;
        int bearing;
        uint16_t width;
        uint8_t quality;
        int slant;
    };
    uint8_t bytes[9]; // around 9 or 10 bytes depending on the struct above
} Lidar;

Lidar lidar;

mcp2515_can CAN(49); // chip selection pin for CAN. 53 for mega, 49 for our new low level board
/*************************** LEO END ******************************/

#define DEBUG true // do not use Serial to print any text during scan. Printing too much will cause this code to miss new scans

// Sweep sensor
Sweep sweep(Serial1);

void enablePower(void)
{
    digitalWrite(POWER_PIN, HIGH);
    if (DEBUG)
    {
        Serial.println(F("pwr on"));
    }
}

void disablePower(void)
{
    sweep.stopScanning();
    digitalWrite(POWER_PIN, LOW);
    if (DEBUG)
    {
        Serial.println(F("pwr off"));
    }
}

void prettyPrintRect(uint16_t myAngle, uint16_t myDistance)
{
    int angle = myAngle * pow(2, -(NUM_FRACTIONAL_BITS));
    int x = myDistance * cos(radians(angle));
    int y = myDistance * sin(radians(angle));
    Serial.print(String(x) + ",");
    Serial.println(String(y));
    Serial.flush();
}

void prettyPrint(uint16_t myAngle, uint16_t myDistance)
{
    int tenthsDegree = int(myAngle * pow(2, -(NUM_FRACTIONAL_BITS)) * 10);
    Serial.print(String(tenthsDegree) + ",");
    Serial.println(myDistance);
    Serial.flush();
}

void sendToCanBus(Lidar lidarStruct)
{
    if (DEBUG)
    {
        Serial.println("Sending data to CAN BUS...");
    }

    // send CAN message to CAN BUS
    CAN.MCP_CAN::sendMsgBuf(Actual_CANID, 0, 8, (uint8_t *)&lidarStruct);
    delay(1000); // This code might not be needed since it is too long for the buffer to be cleared...

    Serial.println("Messages SENT!");
}

// Receive data from the other high/low level board
// NOTE: This function is not tested yet...
void receiveFromCanBus()
{
    unsigned char len = 0;      // message length
    unsigned char msgBuffer[8]; //8 Bytes buffer to store CAN message
    unsigned int canID = 0;

    // Check if received anything
    if (CAN_MSGAVAIL == CAN.checkReceive())
    {
        CAN.readMsgBuf(&len, msgBuffer); // put the data read into buffer and length
        canID = CAN.getCanId();

        if (canID = HiDrive_CANID) // <--- Change the CAN ID according to where this receiver transmitted the CAN message to.
        {
            Serial.print("HiDrive_CANID received: ");
            Serial.println(canID, HEX);
        }
        else if (canID == HiStatus_CANID)
        {
            Serial.print("HiStatus_CANID received: ");
            Serial.println(canID, HEX);
        }
        else if (canID == RCStatus_CANID)
        {
            Serial.print("RCStatus_CANID received: ");
            Serial.println(canID, HEX);
        }
        else if (canID == LowStatus_CANID)
        {
            Serial.print("LowStatus_CANID received: ");
            Serial.println(canID, HEX);
        }
        else if (canID == RCDrive_CANID)
        {
            Serial.print("RCDrive_CANID received: ");
            Serial.println(canID, HEX);
        }
        else if (canID == Actual_CANID)
        {
            Serial.print("Actual_CANID received: ");
            Serial.println(canID, HEX);
        }
        else
        {
            Serial.print("Unexpected CAN ID received: ");
            Serial.println(canID, HEX);
        }

        // Process incoming data (This step should be in the if/else statement above according to each if/else...)
        int resultFromCanBUS = (unsigned int)(msgBuffer[3] << 24) | (msgBuffer[2] << 16) | (msgBuffer[1] << 8) | (msgBuffer[0]);
        Serial.print("ACK msg from CAN BUS: ");
        Serial.println(resultFromCanBUS, DEC);
        Serial.println("Message received from the CAN BUS! Finished...");
    }
}

void setup()
{
    long setupStart = millis();
    // Serial
    Serial.begin(SERIAL_BAUD_RATE);
    // Serial1
    Serial1.begin(SERIAL_BAUD_RATE);

    // Leo: Inital CAN bus with 500KBPS baud rate (CAN_500KBPS is the baud rate)
    while (CAN_OK != CAN.begin(CAN_500KBPS))
    {
        if (DEBUG)
        {
            Serial.println("CAN BUS Shield init fail!!!");
            Serial.println("Re-initializing...");
        }
        delay(100);
    }
    if (DEBUG)
    {
        Serial.println("CAN BUS Shield init OK!");
    }
    // Leo: END

    // Power Enable pin
    pinMode(POWER_PIN, OUTPUT);
    enablePower();
    // Sync / Device Ready pin
    pinMode(SYNC_PIN, INPUT);
    sweep.reset();
    if (DEBUG)
    {
        Serial.println(F("reset"));
    }
    // Wait until motor speed has stabilized
    if (!sweep.getMotorReady())
    {
        sweep.waitUntilMotorReady();
    }
    if (DEBUG)
    {
        Serial.println(F("motor on"));
    }
    // Set motor speed
    if (sweep.getMotorSpeed() != MOTOR_SPEED_HZ)
    {
        sweep.setMotorSpeed(MOTOR_SPEED_CODE);
    }
    // Wait until motor speed has stabilized
    if (!sweep.getMotorReady())
    {
        sweep.waitUntilMotorReady();
    }
    if (DEBUG)
    {
        Serial.println(F("motor ready"));
    }
    // Set sample rate
    if (sweep.getSampleRate() != SAMPLE_RATE_HZ)
    {
        sweep.setSampleRate(SAMPLE_RATE_CODE);
    }
    // Begin taking readings
    if (!sweep.isScanning())
    {
        sweep.startScanning();
    }
    if (DEBUG)
    {
        Serial.println(F("laser scanning!"));
    }
    if (DEBUG)
    {
        Serial.println("motorHz:" + String(MOTOR_SPEED_HZ));
    }
    if (DEBUG)
    {
        Serial.println("scanHz:" + String(SAMPLE_RATE_HZ));
    }
    int duration = (millis() - setupStart) / 1000.0;
    if (DEBUG && (duration >= 1))
    {
        Serial.println("Setup (s): " + String(duration));
    }
    bool sync = false;
    while (!sync)
    {
        // wait until 0 degrees so we begin on a new scan
        sync = digitalRead(SYNC_PIN);
    }
}

uint16_t segmentStart[2];
uint16_t segmentEnd[2];

void loop()
{
    static bool scanFinished = true;
    static bool newSegment = true;
    bool hadReading = false;
    bool insideScanAngles = false;
    bool goodSignal = false;
    // Get reading if available
    ScanPacket reading = sweep.getReading(hadReading);
    uint16_t angle = reading.getAngleRaw();
    uint16_t signalStrength = reading.getSignalStrength();
    uint16_t distance = reading.getDistanceCentimeters();

    if (angle >= R_ANGLE_FIXEDP && angle <= L_ANGLE_FIXEDP)
    {
        insideScanAngles = true;
    }
    if (signalStrength > NOISE_FLOOR && distance > 1 && distance < 4000)
    {
        goodSignal = true;
    }

    if (hadReading && goodSignal && insideScanAngles)
    {
        // we are actively scanning
        scanFinished = false;
        if (newSegment)
        {
            // set segment end and start to current scan
            segmentStart[0] = angle;
            segmentEnd[0] = angle;
            segmentStart[1] = distance;
            segmentEnd[1] = distance;
            prettyPrintRect(angle, distance);
            newSegment = false;
        }
        else
        {
            // update the segment end data
            segmentEnd[0] = angle;
            segmentEnd[1] = distance;
        }
        // now test delta
        int delta = segmentEnd[1] - segmentStart[1];
        if (abs(delta) > MAX_DELTA)
        {
            // we add data pairs as a segment and reset "newSegment"
            prettyPrintRect(angle, distance);
            newSegment = true;
        }
    }
    if (hadReading && !insideScanAngles && !scanFinished)
    {
        // we have a data reading
        // we are out of the scan angles
        // we did not send scan segments
        // this means we are at the end of the scan and can transmit data
        if (!newSegment)
        {
            // we are not at the end of a segment, need to end it
            prettyPrintRect(angle, distance);
            newSegment = true;
        }
        // send scan data here
        scanFinished = true;
    }
}

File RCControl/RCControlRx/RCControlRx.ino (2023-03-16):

/*
    --- References and Acknowledgements ---
    Combine and Update RC control code written by Joe Breithaupt from path: elcano/RadioControl/RadioControl.ino
    https://www.instructables.com/id/How-to-control-Arduino-with-RC-receiver-in-10-minu/
    https://www.arduino.cc/en/Reference/Servo
    https://www.sparkfun.com/tutorials/348
*/
#include "RCControlRX.h"      // <---- Local .h file
// #include <mcp_can.h>          // <---- Import from another library: Seeed-Studio/CAN-BUS-Shield
// #include <mcp_can_dfs.h>      //       (install Library from Arduino, search for "Can-Bus-Shield")
#include <mcp2515_can.h>        // <---- Import from library: Seed-Studio/CAN-BUS-Shield
#include <mcp2515_can_dfs.h>    // <---- Import from library: Seed-Studio/CAN-BUS-Shield
#include <Can_Protocol.h>     // <---- Import from path: elcano/Elcano_C2_LowLevel/Can_Protocol.h
#include <SettingsTemplate.h> // <---- Import from path: elcano/libraries/Settings/SettingsTemplate.h

mcp2515_can CAN(CAN_PIN); // chip selection pin for CAN. 53 for mega, 49 for our new low level board

String logger;
unsigned long now = 0;
unsigned long currTime = 0;
unsigned long duration = 0;
ReceiverData receiverData;
volatile bool RC_Done[RC_NUM_SIGNALS];
volatile unsigned long RC_rise[RC_NUM_SIGNALS];
volatile unsigned long RC_elapsed[RC_NUM_SIGNALS];
unsigned long rc_throttle, rc_turn, rc_reverse, rc_rudd, rc_ebrake, rc_auto;

// Pre-declare functions
void waitInputPWM();
void debugPacket();
void sendToCanBus(ReceiverData message);
void receiveFromCanBus();

// Pre-define attachInterrupt functions
void ISR_TURN_rise();
void ISR_AUTO_rise();
void ISR_ESTOP_rise();
void ISR_GO_rise();
void ISR_REVS_rise();
void ISR_RUDD_rise();
void ISR_GO_fall();
void ISR_TURN_fall();
void ISR_AUTO_fall();
void ISR_ESTOP_fall();
void ISR_REVS_fall();
void ISR_RUDD_fall();


/***********************************************
 *************** SETUP FUNCTIONS ***************
 ***********************************************/
void setup()
{
    if (DEBUG)
    {
        Serial3.begin(UART_BAUDRATE);
        while (!Serial3)
        {
            // wait until Serial3 initialize
        }
        Serial3.println("** RecX Init at " + String(UART_BAUDRATE));
        Serial3.println("Setup Complete!");
    }

    // Initialize arrays to hold data coming from the RC
    receiverData.newData = false;
    for (int i = 0; i < RC_NUM_SIGNALS; i++)
    {
        RC_rise[i] = INVALID_DATA;
        RC_elapsed[i] = INVALID_DATA;
        RC_Done[i] = 0;
    }

    // Initialize attachInterrupt functions to take care of changes from the RC-controller (similar to Async)
    attachInterrupt(digitalPinToInterrupt(IRPT_AUTO), ISR_AUTO_rise, RISING);
    attachInterrupt(digitalPinToInterrupt(IRPT_REVS), ISR_REVS_rise, RISING);
    attachInterrupt(digitalPinToInterrupt(IRPT_TURN), ISR_TURN_rise, RISING);
    attachInterrupt(digitalPinToInterrupt(IRPT_ESTOP), ISR_ESTOP_rise, RISING);
    attachInterrupt(digitalPinToInterrupt(IRPT_THROTTLE), ISR_GO_rise, RISING);
    // attachInterrupt(digitalPinToInterrupt(IRPT_RUDD), ISR_RUDD_rise, RISING); // <---- Commented out if needed to use this pin

    // Inital CAN bus with 500KBPS baud rate (CAN_500KBPS is the baud rate)
    while (CAN_OK != CAN.begin(CAN_500KBPS))
    {
        if (DEBUG)
        {
            Serial3.println("CAN BUS Shield init fail!!!");
            Serial3.println("Re-initializing...");
        }
        delay(100);
    }
    if (DEBUG)
    {
        Serial3.println("CAN BUS Shield init OK!");
    }
}

/***********************************************
 *************** LOOP FUNCTIONS ****************
 ***********************************************/
void loop()
{
    // check for new data
    waitInputPWM();

    // NOTE: This is temporary and should be used somewhere wherever the data is consumed
    // (data transmitted from this RC-receiver to other Board, processed there and transmitted back here.
    // This is the process the DEBUG below is trying to simulate)
    if (DEBUG)
    {
        if (receiverData.newData == true)
        {
            if (receiverData.ebrakeOn == true)
            {
                rc_ebrake = 1;
            }
            else
            {
                rc_ebrake = 0;
            }

            if (receiverData.autoOn == true)
            {
                rc_auto = 1;
            }
            else
            {
                rc_auto = 0;
            }

            if (receiverData.reverse == true)
            {
                rc_reverse = 1;
            }
            else
            {
                rc_reverse = 0;
            }
            rc_throttle = receiverData.throttle;
            rc_turn = receiverData.turnAngle;
            debugPacket(); // Print out to the screen

            // NOTE: THIS IS IMPORTANT LINE BELOW, SHOULD NOT BE UNDER DEBUG!!!! NEED TO BE USED IN CONSUMER CODE!!!!
            // This is where the Receiver gets the ACK signal from the other boards that used this data and response back through CAN BUS Protocal
            receiveFromCanBus();
            receiverData.newData = false;
        }
    }
}

/***********************************************
 *************** HELPER FUNCTIONS **************
 ***********************************************/

// Wait until the data comes back from the attachInterrupt().
// This function is going to process all the data gather and parse it into a struct: receiverData
void waitInputPWM()
{
    // NOTE: Data received from the RC will be fluctuated from 1000 to 1800.
    // By having threshold, we know when the switches are flipped
    const int THRESHOLD = 1500;
    const int REVS_THRESHOLD = 2090;
    if (RC_Done[RC_ESTP] == true)
    {
        receiverData.ebrakeOn = (RC_elapsed[RC_ESTP] > THRESHOLD ? true : false);
        receiverData.newData = true;
        // Reset everything to pick up new pulses
        RC_Done[RC_ESTP] = false;
    }

    if (RC_Done[RC_AUTO] == true)
    {
        receiverData.autoOn = (RC_elapsed[RC_AUTO] > THRESHOLD ? true : false);
        receiverData.newData = true;
        // Reset everything to pick up new pulses
        RC_Done[RC_AUTO] = false;
    }

    if (RC_Done[RC_THROTTLE] == true)
    {
        receiverData.throttle = RC_elapsed[RC_THROTTLE];
        receiverData.newData = true;
        // Reset everything to pick up new pulses
        RC_Done[RC_THROTTLE] = false;
    }

    if (RC_Done[RC_TURN] == true)
    {
        receiverData.turnAngle = RC_elapsed[RC_TURN];
        receiverData.newData = true;
        // Reset everything to pick up new pulses
        RC_Done[RC_TURN] = false;
    }

    if (RC_Done[RC_REVS] == true)
    {
        receiverData.reverse = (RC_elapsed[RC_REVS] >= REVS_THRESHOLD ? true : false);
        receiverData.newData = true;
        // Reset everything to pick up new pulses
        RC_Done[RC_REVS] = false;
    }

    sendToCanBus(receiverData); // Send current data formatted to CAN BUS protocol
}
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

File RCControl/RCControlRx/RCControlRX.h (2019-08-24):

#define UART_BAUDRATE 115200
#define CAN_PIN 3
#define DEBUG_EN 1

// MAPPING pins of the RC-receiver - SAMD21
#define AUX_PIN 7      // AUX  - D7
#define GEAR_PIN 8     // GEAR - D8
#define RUDD_PIN 0     // RUDD - D0
#define ELEV_PIN 1     // ELEV - D1
#define AILE_PIN 6     // AILE - D6
#define THROTTLE_PIN 9 // THRO - D9

#define DEBUG 1 // Prints debugging info to serialUSB, can impact loop time                         \
                // WARNING: when true (!0), you must connect USB to allow hardware reset, otherwise \
                // SAMD21 Arduino will do nothing*/

#define TX_LED_LINK 6 // LED pins on the transmitter
#define NO_PACKAGE -1 // LED pins on the transmitter

// #define ProcessFallOfINT(Index) RC_elapsed[Index] = (micros() - RC_rise[Index])
// #define ProcessRiseOfINT(Index) RC_rise[Index] = micros()
#define ProcessFallOfINT(Index) RC_elapsed[Index] = (micros() - RC_rise[Index])
#define ProcessRiseOfINT(Index) RC_rise[Index] = micros()
#define INVALID_DATA 0L  // This is a value that the RC controller can't produce.
#define RC_NUM_SIGNALS 7 // How many RC signals we receive (USED TO BE 7)

// ----- IMPORTED FROM THE SettingsTemplate.h ---------
#define RC_TURN 1
#define RC_AUTO 2
#define RC_REVS 3
#define RC_ESTP 4
#define RC_THROTTLE 5
#define RC_RUDD 6

// The numbers defined below are SAMD21 Pins
#define IRPT_RUDD 1     // RUDD_PIN     - channel 4
#define IRPT_REVS 0     // ELEV_PIN     - channel 3
#define IRPT_AUTO 9     // AUX_PIN      - channel 6
#define IRPT_ESTOP 6    // GEAR_PIN     - channel 5
#define IRPT_THROTTLE 7 // THROTTLE_PIN - channel 1
#define IRPT_TURN 8     // AILE_PIN     - channel 2
// ----- IMPORTED FROM THE SettingsTemplate.h ---------

// ----- IMPORTED FROM THE Can_Protocal.h (path: elcano/Elcano_C2_lowlevel/Can_Protocal.h)---------
#define RCStatus_CANID 0x50
#define HiStatus_CANID 0x100
#define LowStatus_CANID 0x200
#define RCDrive_CANID 0x300
#define HiDrive_CANID 0x350
#define Actual_CANID 0x500
    // ----- IMPORTED FROM THE Can_Protocal.h (path: elcano/Elcano_C2_lowlevel/Can_Protocal.h)---------

    // 32 bits = 4 bytes
    // 8 bits = 1 byte
    typedef union {
    struct
    {
        uint32_t throttle;
        uint32_t turnAngle;
        uint8_t ebrakeOn;
        uint8_t autoOn;
        uint8_t reverse; // Future Stuff
        uint8_t newData;
    };
    uint8_t bytes[12]; // The length of this byte buffer is dependded on the amount of Bytes in the struct above
} ReceiverData;

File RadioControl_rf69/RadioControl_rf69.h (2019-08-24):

#ifndef RC_RF69_H
#define RC_RF69_H

#define UART_BAUDRATE 115200
#define RF69_FREQ_MHZ 915.0

// The encryption key has to be the same for transmitter and receiver
uint8_t key[] = {0x01, 0x02, 0x03, 0x04, 0x05, 0x06, 0x07, 0x08,
                 0x07, 0x06, 0x05, 0x04, 0x03, 0x02, 0x01, 0x00};

typedef union {
  struct
  {
    uint16_t throttle;
    uint16_t turn;
    uint8_t ebrake;
    uint8_t autonomous;
    uint8_t rssi; // "The current RSSI value in units of 0.5dB", negative
  };
  uint8_t bytes[5]; // The length of this byte buffer is dependded on the amount of Bytes in the struct above
} DataFromTransmitter;

typedef struct
{
  uint8_t rssi; // "The current RSSI value in units of 0.5dB", negative
} DataFromReceiver;

// transmitter input pins
#define TURN_PIN A3     // joystick 2 L/R
#define THROTTLE_PIN A2 // joystick 1 U/D
#define INTERRUPT_PIN 2
#define AUTO_PIN 5
#define EBRAKE_PIN 4
#define REVERSE_PIN 20

// ----- IMPORTED FROM THE Can_Protocal.h (path: elcano/Elcano_C2_lowlevel/Can_Protocal.h)---------
#define RCStatus_CANID 0x50
#define HiStatus_CANID 0x100
#define LowStatus_CANID 0x200
#define RCDrive_CANID 0x300
#define HiDrive_CANID 0x350
#define Actual_CANID 0x500
// ----- IMPORTED FROM THE Can_Protocal.h (path: elcano/Elcano_C2_lowlevel/Can_Protocal.h)---------



// LED pins on the transmitter
#define TX_LED_LINK 6

// other outputs
#define SS_PIN 10
/* pins 11 - 13 are reserved for SPI */

#endif

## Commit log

2015-03-13 added arduino files
2019-06-10 Add Bluetooth and RC code. Bluetooth is completed with CAN BUS (CAN BUS - Not tested yet). RC is being developed.
2019-08-24 End of Summer 2019 commit (Maneuverability Team documents and working code
    [ScanseSweepv1.1.sch, Transceiver_Board_V_1.5.sch, Transceiver_Board_V_1_5.brd]
2019-08-27 Added electronics files for transceiver & sweep
    [ScanseSweepv1.1.brd, ScanseSweepv1.1.sch, SweepBoard_BoM.xlsx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]
2019-12-13 Fall2019 Transciever update
    [Transceiver_BoM_Fall2019.xlsx]
2023-03-04 updated CAN-BUS-Shield library and files to compile

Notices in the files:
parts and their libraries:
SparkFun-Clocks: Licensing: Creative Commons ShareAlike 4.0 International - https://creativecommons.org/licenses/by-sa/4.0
